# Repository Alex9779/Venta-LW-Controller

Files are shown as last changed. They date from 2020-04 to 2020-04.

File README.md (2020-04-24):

# Venta LW Controller
This project contains the electronics design, assembly and programming instructions for a board to be used in Venta airwashers of '[5 Series Classic](https://venta-usa.com/product-category/airwashers/5-series-classic/)' or '[LW Original](https://www.venta-luftwaescher.de/shop/alle-luftwaescher/original-bis-75-m2/)'  , see [Venta USA](https://venta-usa.com/) or [Venta Germany](https://www.venta-luftwaescher.de/).

The control board is based on an ESP32 module by [Espressif](https://www.espressif.com/) in particular an [ESP32-WROOM-32](http://espressif.com/zh-hans/products/hardware/esp-wroom-32/overview) module.

The intention of this project is to be able to control Venta airwashers remotely, in my case using [ESPHome](https://esphome.io/index.html) and [Home-Assistant](https://www.home-assistant.io/), that is turn it on and off and select the speed and also get information if it is on or off, what the current speed is and if it has an error.

But it is possible to use other tools to generate a firmware or write a completly own firmware for special needs.

## Board components
The board has six components:

1. ESP32 module
2. connector to the Venta airwasher
3. power supply circuit to transform 24V to 3.3V
4. button control circuit using BSS138 N-MOSFETs
5. LED state detection circut using diodes to block current to the ESP32's logic circuit
6. maintenance connector and buttons

## LED state detection circuit design and remarks
To detect the state of the LEDs and so the state of the airwasher diodes are used and the logic input of the ESP are set to HIGH in the PIN configuration of the firmware becuase of the design of the Venta control circuits.

The LEDs are under constant voltage and the control circuit closes when an LED shall be activated. Because of that we have constant 24V if and LED is off. Using a voltage divider to get that down to the ESP32's logic level is not possible because a voltage divider closes the circuit constantly even with very high resistor a little current flows throught the LEDs and as a result the LEDs shine a littel.

So the idea was to prevent current to the ESP32, set the PINs to HIGH and when the Venta controlle closes the circuit the PIN is pulled low.

In fact this works for the blue LEDs but not for the red one. So detecting error case is moved to the firmware logic. That relies on the fact that if the airwasher is on normally one of the speeds LEDs is lit, if not then the error LED is lit.

## Needed materials
| Amount | Part | used model |
| :----: | --- | --- |
| 1 | PCB |
| 1 | ESP32-WROOOM-32 module |
| 1 | IDC plug for ribbon cable, 10 pins, 1.27mm cable pitch, 2.54mm contacts pitch | AMPHENOL T812110A101CEU |
| 1 | IDC socket, 10 pins, 2.54mm contacts pitch | AMPHENOL T821110A1S100CEU |
| 1 | DC-DC buck converter, SO8, Uout 3.3V, Uin minimal 24V | Texas Instruments LM2674M-3.3/NOPB |
| 1 | tantalum capacitor, 22uF, 35VDC, Case D | AVX TAJD226K035RNJ |
| 1 | tantalum capacitor, 100uF, 10VDC, Case C | AVX TPSC107M010R0100 |
| 1 | Schottky diode, 30V | DIODES INCORPORATED B130-13-F |
| 1 | wire inductor, 68uH, 12x12x6mm | FERROCORE DE1205-68 |
| 1 | ceramic capacitor, 10nF, 0603 |
| 1 | resistor, 10K, 0603 |
| 2 | ceramic capacitor, 100nF, 0603 |
| 1 | ceramic capacitor, 10uF, 0603 |
| 2 | resistor, 470R, 0603 |
| 2 | resistor, 4K7, 0603 |
| 2 | N-MOSFET, SOT-23 | BSS138 |
| 5 | diode, SOD-323 | 1N4148WS |
| 1 | pin header, 4 pins, 2.54mm pitch |
| 2 | TACT buttons, 6mm |

## Firmware
As described before I use ESPhome to generate a firmware and Home-Assistant to control the devices.

A sample ESPHome configuration to generate a firmware can be found in the 'ESPHome configuration sample' directoy of this repository. This sample also includes the configuration for an external Bluetooth temperature and humidity sensor [Xiaomi CGG1](https://esphome.io/components/sensor/xiaomi_cgg1.html).

## Installation
To installe the addtional PCB you have remove the fan module from your Venta airwasher and open it. With a flat screwdriver this is no real problem and it can be done without any damage, take you time and wiggle and bend the case also a little to get the points where it is clipped together, once you got the trick it is easy.

Here a Venta LW45:

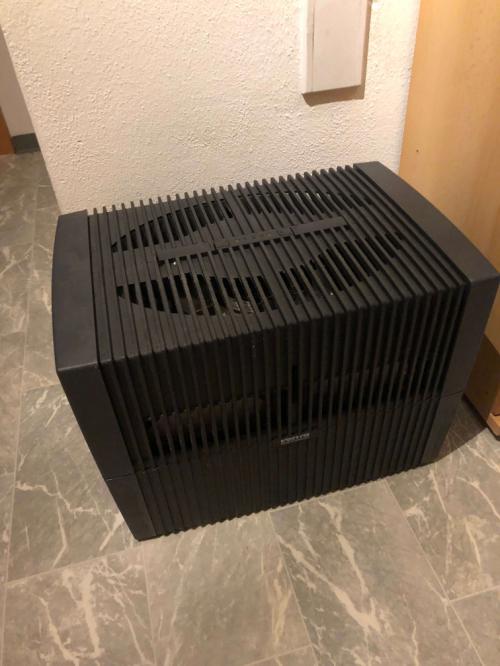
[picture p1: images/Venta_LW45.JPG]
Venta LW45


Open the cover:

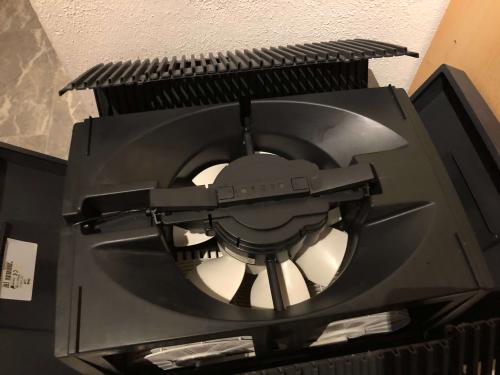
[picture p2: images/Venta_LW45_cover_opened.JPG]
Venta LW45 cover opened


Remove the fan module:

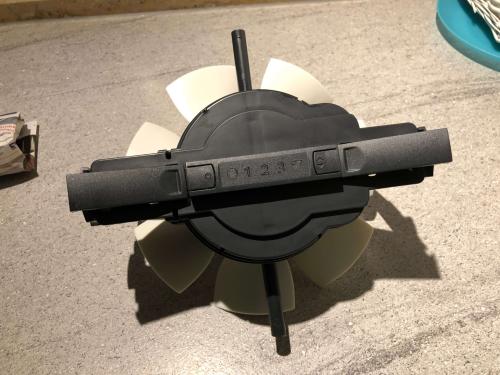
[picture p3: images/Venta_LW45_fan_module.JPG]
Venta LW45 fan module


Open the fan module:

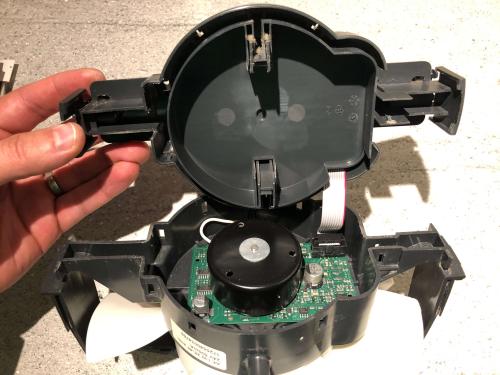
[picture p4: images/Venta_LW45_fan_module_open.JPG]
Venta LW45 fan module open


Remove the seperator:

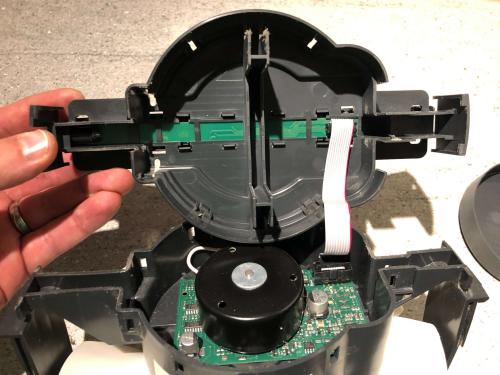
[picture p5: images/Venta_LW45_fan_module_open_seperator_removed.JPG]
Venta LW45 fan module open seperator removed


Remove the ribbon cable from the main board:

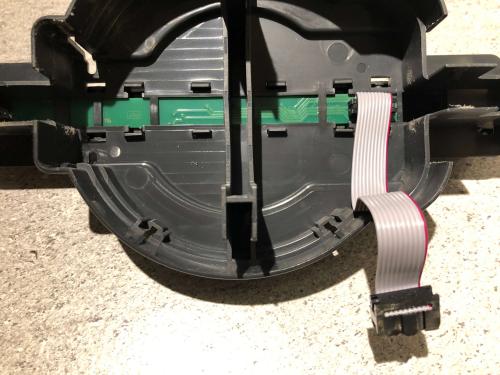
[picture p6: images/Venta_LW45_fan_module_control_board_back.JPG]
Venta LW45 fan module control board back


Add the addtional plug to the ribbon cable:

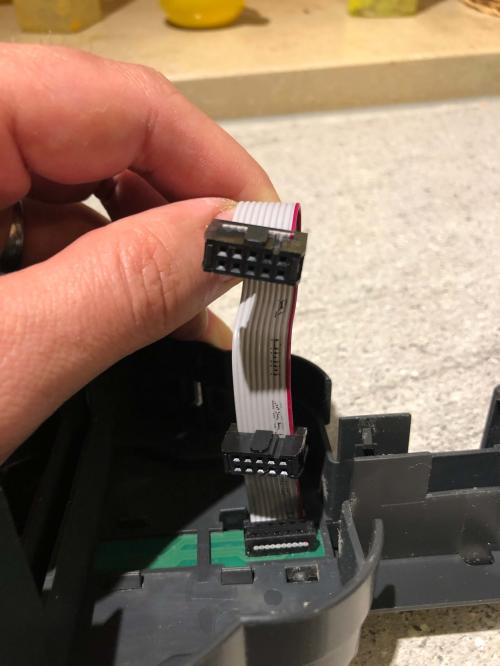
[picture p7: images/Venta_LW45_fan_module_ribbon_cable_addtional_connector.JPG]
Venta LW45 fan module ribbon cable addtional connector


Put the PCB in the cover and connect the cable:

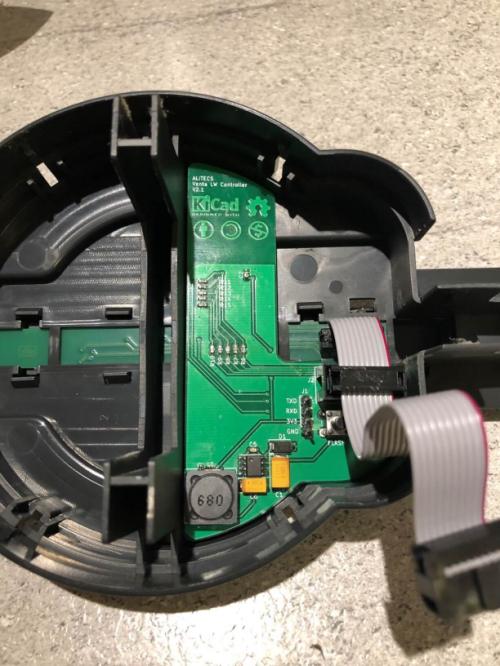
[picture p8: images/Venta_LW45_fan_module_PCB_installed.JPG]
Venta LW45 fan module PCB installed


Add the seperator, connect the cable to the main board and close the fan module.

You're done!

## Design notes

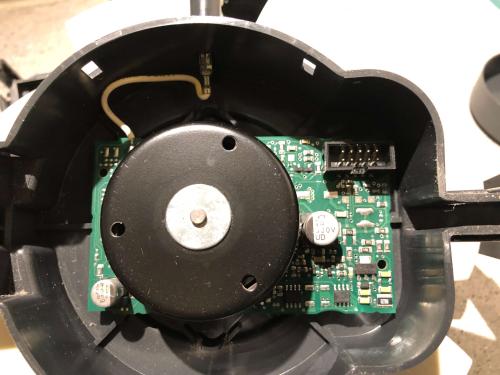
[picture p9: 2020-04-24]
images/Venta_LW45_fan_module_main_board.JPG

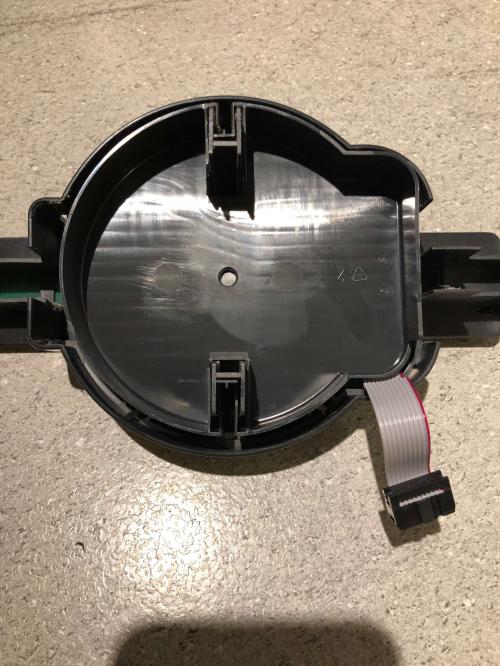
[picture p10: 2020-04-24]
images/Venta_LW45_fan_module_top_with_seperator.JPG

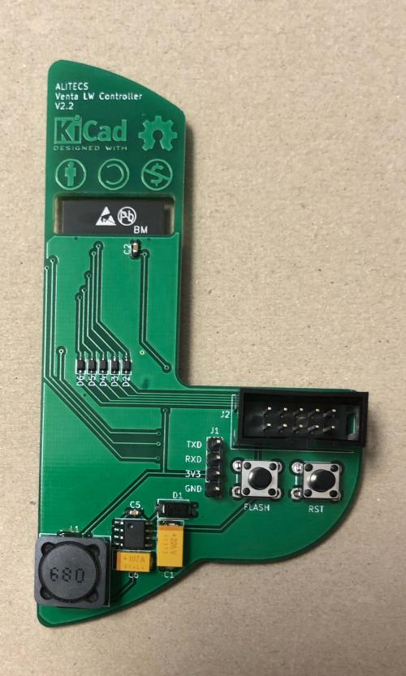
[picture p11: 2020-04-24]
images/PCB_v2.2 front.jpg

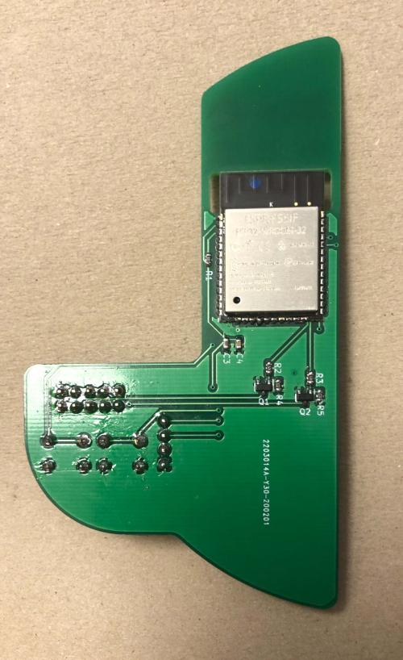
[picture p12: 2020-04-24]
images/PCB_v2.2 back.jpg

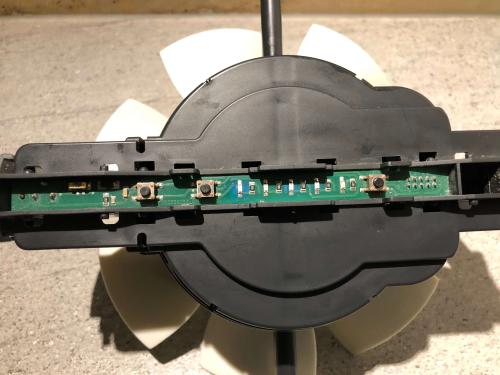
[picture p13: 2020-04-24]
images/Venta_LW45_fan_module_control_board_front.JPG

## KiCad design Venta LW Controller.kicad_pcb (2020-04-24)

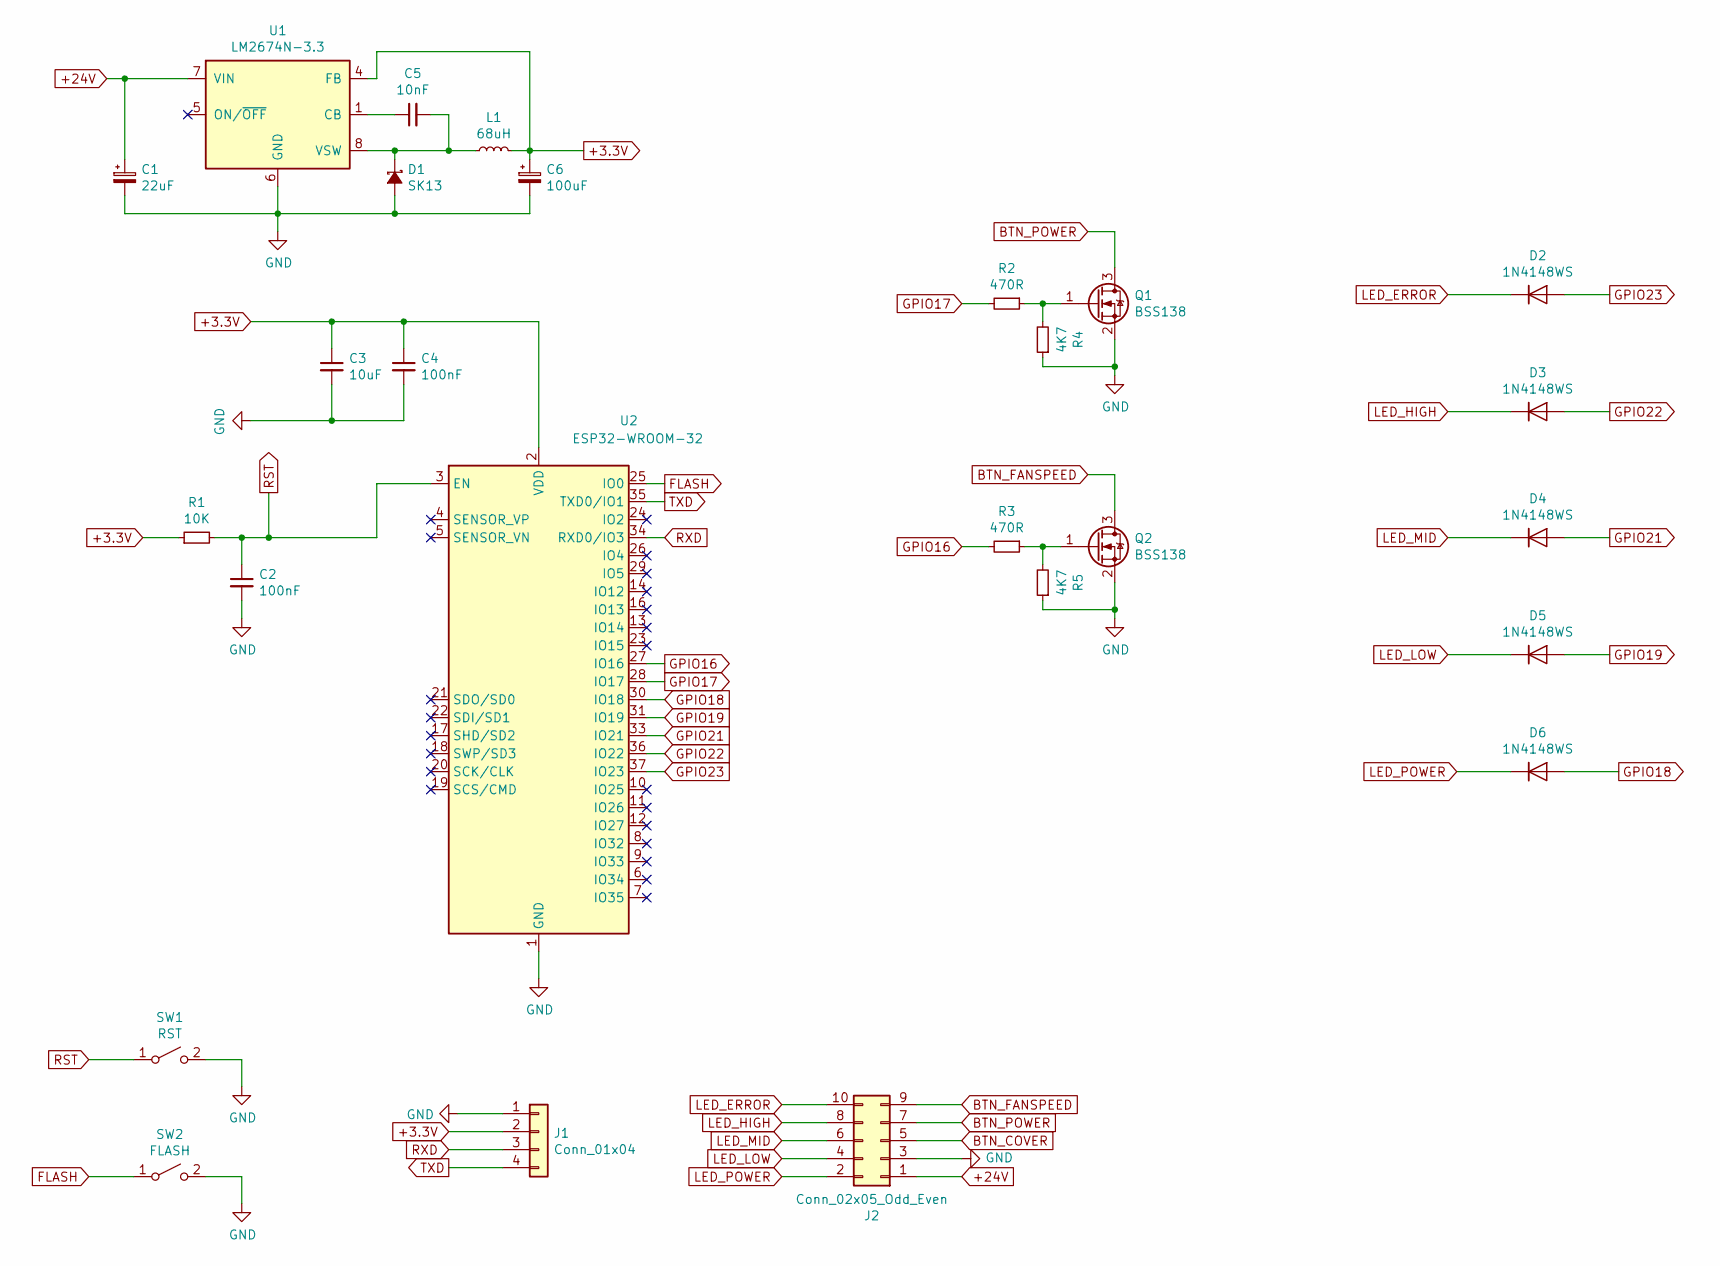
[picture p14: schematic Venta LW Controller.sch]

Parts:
C1: 22uF; CP_EIA-7343-31_Kemet-D
C2, C4: 100nF; C_0603_1608Metric
C3: 10uF; C_0603_1608Metric
C5: 10nF; C_0603_1608Metric
C6: 100uF; CP_EIA-6032-28_Kemet-C
D1: SK13; D_SMA
D2, D3, D4, D5, D6: 1N4148WS; D_SOD-323
J1: Conn_01x04; PinHeader_1x04_P2.54mm_Vertical
J2: Conn_02x05_Odd_Even; IDC-Header_2x05_P2.54mm_Vertical
L1: 68uH; L_12x12mm_H6mm
Q1, Q2: BSS138; SOT-23
R1: 10K; R_0603_1608Metric
R2, R3: 470R; R_0603_1608Metric
R4, R5: 4K7; R_0603_1608Metric
SW1: RST; SW_PUSH_6mm_H5mm
SW2: FLASH; SW_PUSH_6mm_H5mm
U1: LM2674N-3.3; SOIC-8_3.9x4.9mm_P1.27mm
U2: ESP32-WROOM-32

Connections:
+3.3V: C3.1, C4.1, C6.1, J1.2, L1.2, R1.1, U1.4 (FB), U2.2 (VDD)
+24V: C1.1, J2.1, U1.7 (VIN)
BTN_COVER: J2.5
BTN_FANSPEED: J2.9, Q2.3 (D)
BTN_POWER: J2.7, Q1.3 (D)
FLASH: SW2.1 (A), U2.25 (IO0)
GND: C1.2, C2.2, C3.2, C4.2, C6.2, D1.2 (A), J1.1, J2.3, Q1.2 (S), Q2.2 (S), R4.1, R5.1, SW1.2 (B), SW2.2 (B), U1.6 (GND), U2.1 (GND), U2.15 (GND), U2.38 (GND), U2.39 (GND)
GPIO16: R3.2, U2.27 (IO16)
GPIO17: R2.2, U2.28 (IO17)
GPIO18: D6.2 (A), U2.30 (IO18)
GPIO19: D5.2 (A), U2.31 (IO19)
GPIO21: D4.2 (A), U2.33 (IO21)
GPIO22: D3.2 (A), U2.36 (IO22)
GPIO23: D2.2 (A), U2.37 (IO23)
LED_ERROR: D2.1 (K), J2.10
LED_HIGH: D3.1 (K), J2.8
LED_LOW: D5.1 (K), J2.4
LED_MID: D4.1 (K), J2.6
LED_POWER: D6.1 (K), J2.2
unnamed: C5.1, U1.1 (CB)
unnamed: C5.2, D1.1 (K), L1.1, U1.8 (VSW)
unnamed: Q1.1 (G), R2.1, R4.2
unnamed: Q2.1 (G), R3.1, R5.2
RST: C2.1, R1.2, SW1.1 (A), U2.3 (EN)
RXD: J1.3, U2.34 (RXD0/IO3)
TXD: J1.4, U2.35 (TXD0/IO1)

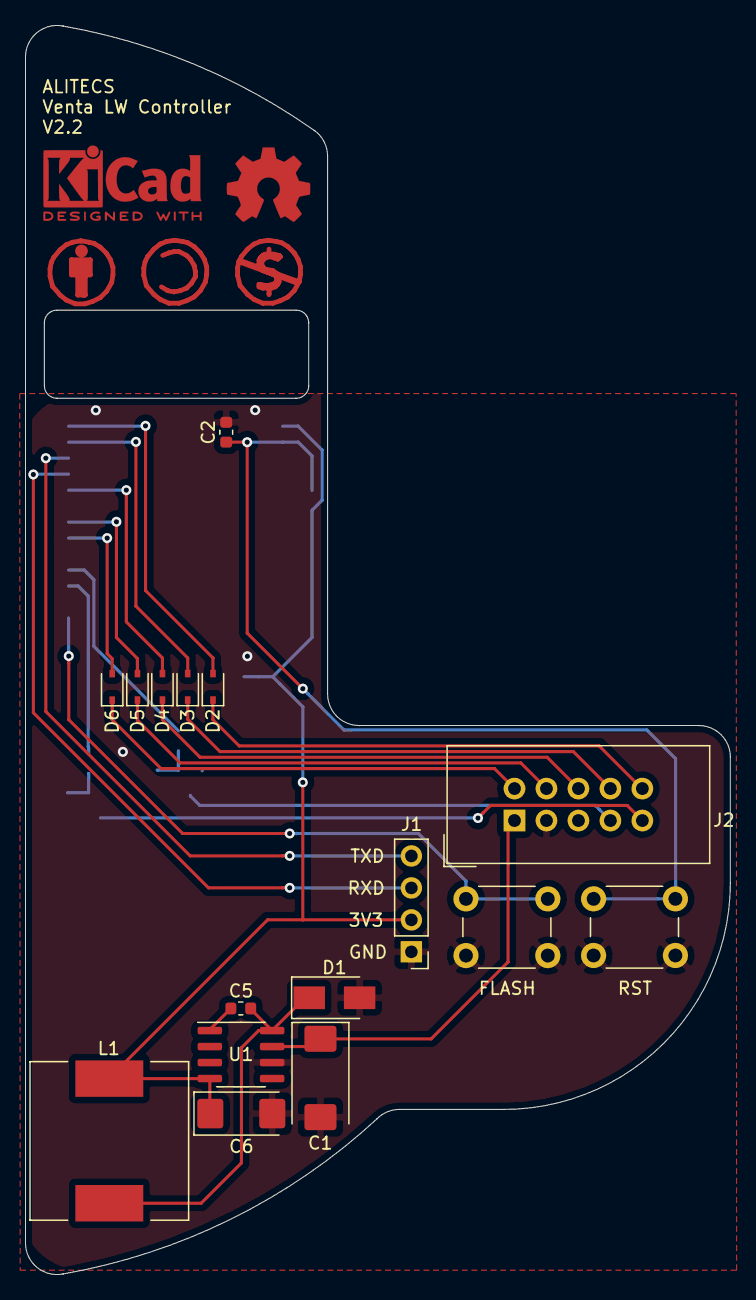
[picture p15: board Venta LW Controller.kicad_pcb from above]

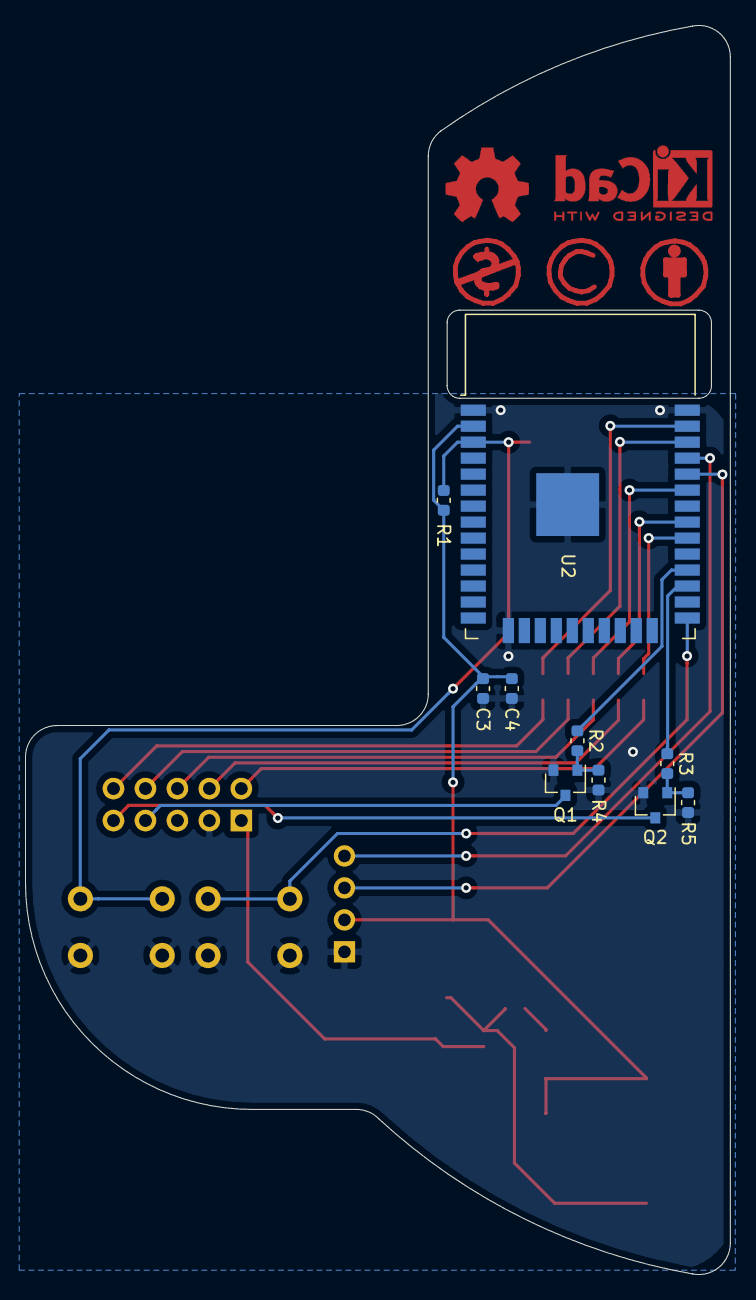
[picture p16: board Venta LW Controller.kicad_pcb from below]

Board: 2 copper layers, 56.0 x 99.2 mm, 26 parts (10 on the bottom side), 25 nets.

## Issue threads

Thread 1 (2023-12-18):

Support for Venta LW45 Comfort Plus

niwi-hh, 2023-12-18:
I own a Venta LW15 Original and a Venta LW45 Comfort Plus.

For my LW15 I already found my own solution based on a Shelly Uni (for push button control) and a Shelly Plug S (for reading the running level by the device's power consumption).

But I wonder if this project would work with my LW45 Comfort Plus. This device has the original design apart from the touch display. Since there are no touch buttons, I can't control the running level by a Shelly Uni. Would it work with this solution here?

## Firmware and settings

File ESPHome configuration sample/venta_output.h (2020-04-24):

#include "esphome.h"
using namespace esphome;
 
const int PIN_SWITCH_FANSPEED = 16;
const int PIN_SWITCH_POWER = 17;
const int PIN_LED_POWER = 18;
const int PIN_LED_LOW = 19;
#if !defined(LW15)
const int PIN_LED_MID = 21;
#endif
const int PIN_LED_HIGH = 22;
 
#if !defined(LW15)
const float LOW_TO_MID = 0.33;
const float MID_TO_HIGH = 0.66;
#else
const float LOW_TO_MID = 0.5;
#endif
 
const int SWITCH_DELAY = 100;
const int SWITCH_INTERVAL = 200;
 
class VentaOutput : public Component, public FloatOutput {
  public:
    void setup() override {
      pinMode(PIN_SWITCH_FANSPEED, OUTPUT); // switch fanspeed
      pinMode(PIN_SWITCH_POWER, OUTPUT); // switch power
    }
 
    void write_state(float state) override {
      id(sensor_speed).publish_state(state);
 
      if (id(internal_error).state && state != -1) return;
 
      if (state >= 0 && state < LOW_TO_MID) { // switch off
        if (!digitalRead(PIN_LED_POWER)) {
          clickSwitch(PIN_SWITCH_POWER);
        }
      }
      else if (state >= LOW_TO_MID && state < MID_TO_HIGH) { // switch to low
        if (digitalRead(PIN_LED_POWER)) {
          clickSwitch(PIN_SWITCH_POWER);
        }
        while (digitalRead(PIN_LED_LOW)) // pin readings are inverted!
        {
          clickSwitch(PIN_SWITCH_FANSPEED);
          if (id(internal_error).state) {
            break;
          }
        }
      }
#if !defined(LW15)
      else if (state >= MID_TO_HIGH && state < 1) { //switch to mid
        if (digitalRead(PIN_LED_POWER)) {
          clickSwitch(PIN_SWITCH_POWER);
        }
        while (digitalRead(PIN_LED_MID)) // pin readings are inverted!
        {
          clickSwitch(PIN_SWITCH_FANSPEED);
          if (id(internal_error).state) {
            break;
          }
        }
      }
#endif
      else if (state == 1) {
        if (digitalRead(PIN_LED_POWER)) { // switch to high
          clickSwitch(PIN_SWITCH_POWER);
        }
        while (digitalRead(PIN_LED_HIGH)) // pin readings are inverted!
        {
          clickSwitch(PIN_SWITCH_FANSPEED);
          if (id(internal_error).state) {
            break;
          }
        }
      }
    }
 
  private:
    void clickSwitch(int pin) {
      digitalWrite(pin, true);
      delay(SWITCH_DELAY);
      digitalWrite(pin, false);
      delay(SWITCH_INTERVAL);
    }
};

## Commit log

2019-09-14 use usable GPIOs
    [Venta LW Controller.kicad_pcb, Venta LW Controller.sch]
2019-09-14 bumped version
    [Venta LW Controller.kicad_pcb]
2019-09-14 switched to ESP32
    [Venta LW Controller.kicad_pcb, Venta LW Controller.sch]
2019-09-17 updated tracks
    [Venta LW Controller.kicad_pcb]
2019-09-17 added keepout area
    [Venta LW Controller.kicad_pcb]
2019-09-17 corrected circuit and updated layout
    [Venta LW Controller.kicad_pcb, Venta LW Controller.sch]
2019-09-17 corrected circuit
    [Venta LW Controller.sch]
2019-09-18 updated layout
    [Venta LW Controller.kicad_pcb]
2019-09-20 updated package
    [Venta LW Controller.kicad_pcb, Venta LW Controller.sch]
2019-09-26 updated values
    [Venta LW Controller.sch]
2019-09-26 updated parts
    [Venta LW Controller.kicad_pcb, Venta LW Controller.sch]
2019-09-26 added and updated texts
    [Venta LW Controller.kicad_pcb]
2019-09-26 fixed transistor connection
    [Venta LW Controller.kicad_pcb]
2019-09-26 cleaned circuits
    [Venta LW Controller.kicad_pcb]
2019-09-26 rebuilt areas
    [Venta LW Controller.kicad_pcb]
2019-09-27 reworked
    - added correct circuit for BSS138
    - added voltage divider for inputs
    - changed buck converter setup
    [Venta LW Controller.kicad_pcb, Venta LW Controller.sch]
2019-10-07 changed voltage divider to diodes
    [Venta LW Controller.kicad_pcb, Venta LW Controller.sch]
2020-01-31 added cutout around antenna
    [Venta LW Controller.kicad_pcb]
2020-04-24 added ESPHome sample
2020-04-24 refilled and rotated connector
    [Venta LW Controller.kicad_pcb, Venta LW Controller.sch]
